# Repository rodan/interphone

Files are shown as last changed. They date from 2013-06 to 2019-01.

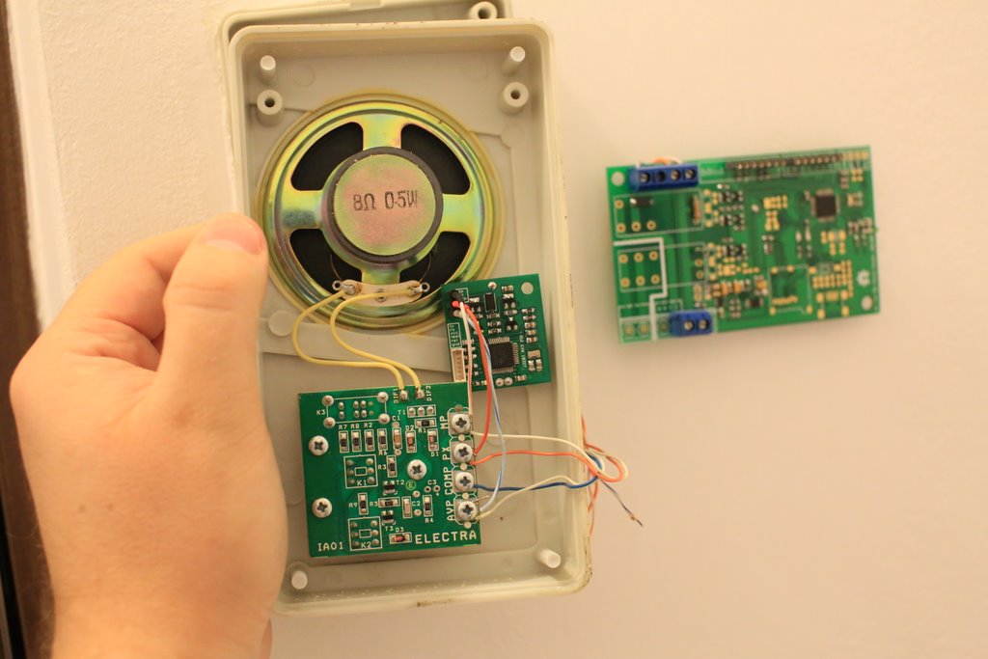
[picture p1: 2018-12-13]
img/DA0B7957.JPG

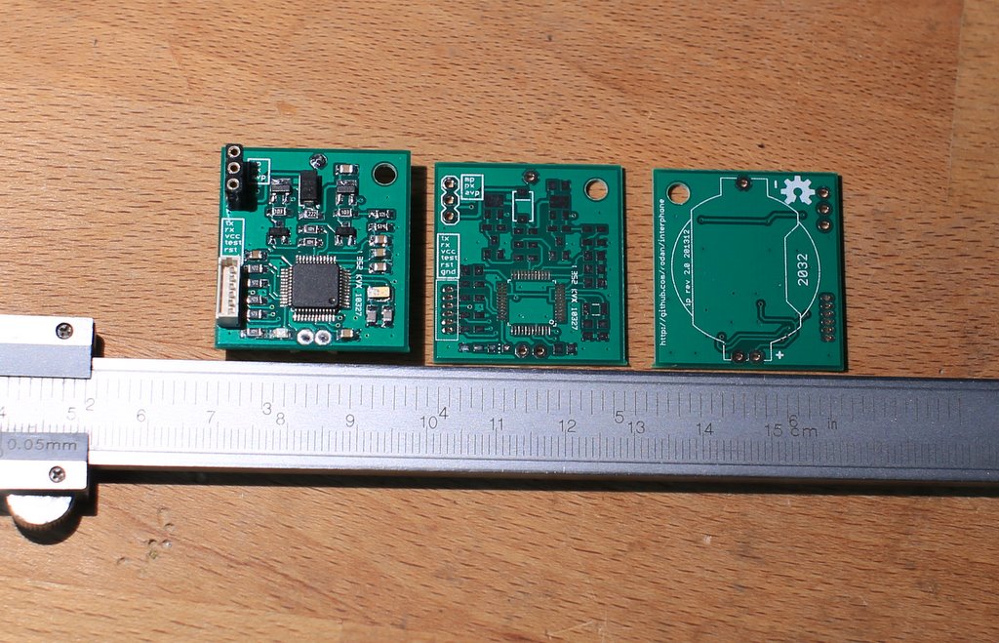
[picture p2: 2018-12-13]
img/DA0B7967.JPG

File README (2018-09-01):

MSP430F5510 based project that ties into the appartment interphone system. in this case it's an Electra IA01.
it allows the owner outside the building to open the door by following a pre-determined list of actions.

if config.h RADIO option (*) is defined then the door opening is triggered by the following actions:
 - call interphone number
 - wait 2s
 - send a radio signal to a receiver that is tied into the project. the receiver should pull P1.2 low on activation.
 - door opens if the signal was received in the defined time window
 If the radio option is not viable due to poor signal/noise ratio another scenario is implemented by deactivating the RADIO ifdef.
 - call interphone number
 - hang up and call again in the software predetermined timeframe
 - door opens

 the first scenario needs one 12v battery, a 12V one channel RC receiver and transmitter. a chronos watch could be used as the RC remote if the topology permits, see [1], [2]. current consumption is about 110uA@12V.
 the second scenario only needs one 3v 2032 Li cell. current consumption is about 1.4uA@3V. the pcb for this one is to be found in hardware/ip_simple.brd

Pinout:
 - P1.1 - 'ring' detector from interphone 'PX'
 - P1.2 - (optional) radio trigger
 - P1.4 - OPEN
 - P1.5 - TALK
 - P1.6 - (optional) power enable for radio rx system

(*) radio-related code removed

 homepage:        https://github.com/rodan/interphone
 author:          Petre Rodan <2b4eda@subdimension.ro>
 license:         GNU GPLv3
 parts of the code were originally forked from the openchronos-ng project [3]. 

 software requirements:

   msp430 toolchain

[1] http://www.ti.com/tool/ez430-chronos
[2] https://github.com/rodan/openchronos-rfsw
[3] http://openchronos-ng.sourceforge.net

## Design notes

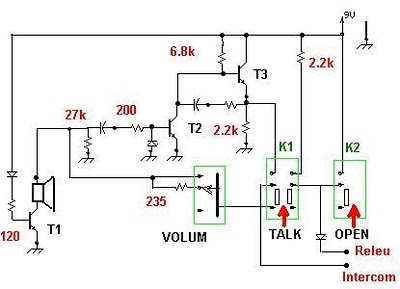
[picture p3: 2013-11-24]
img/electra.jpg

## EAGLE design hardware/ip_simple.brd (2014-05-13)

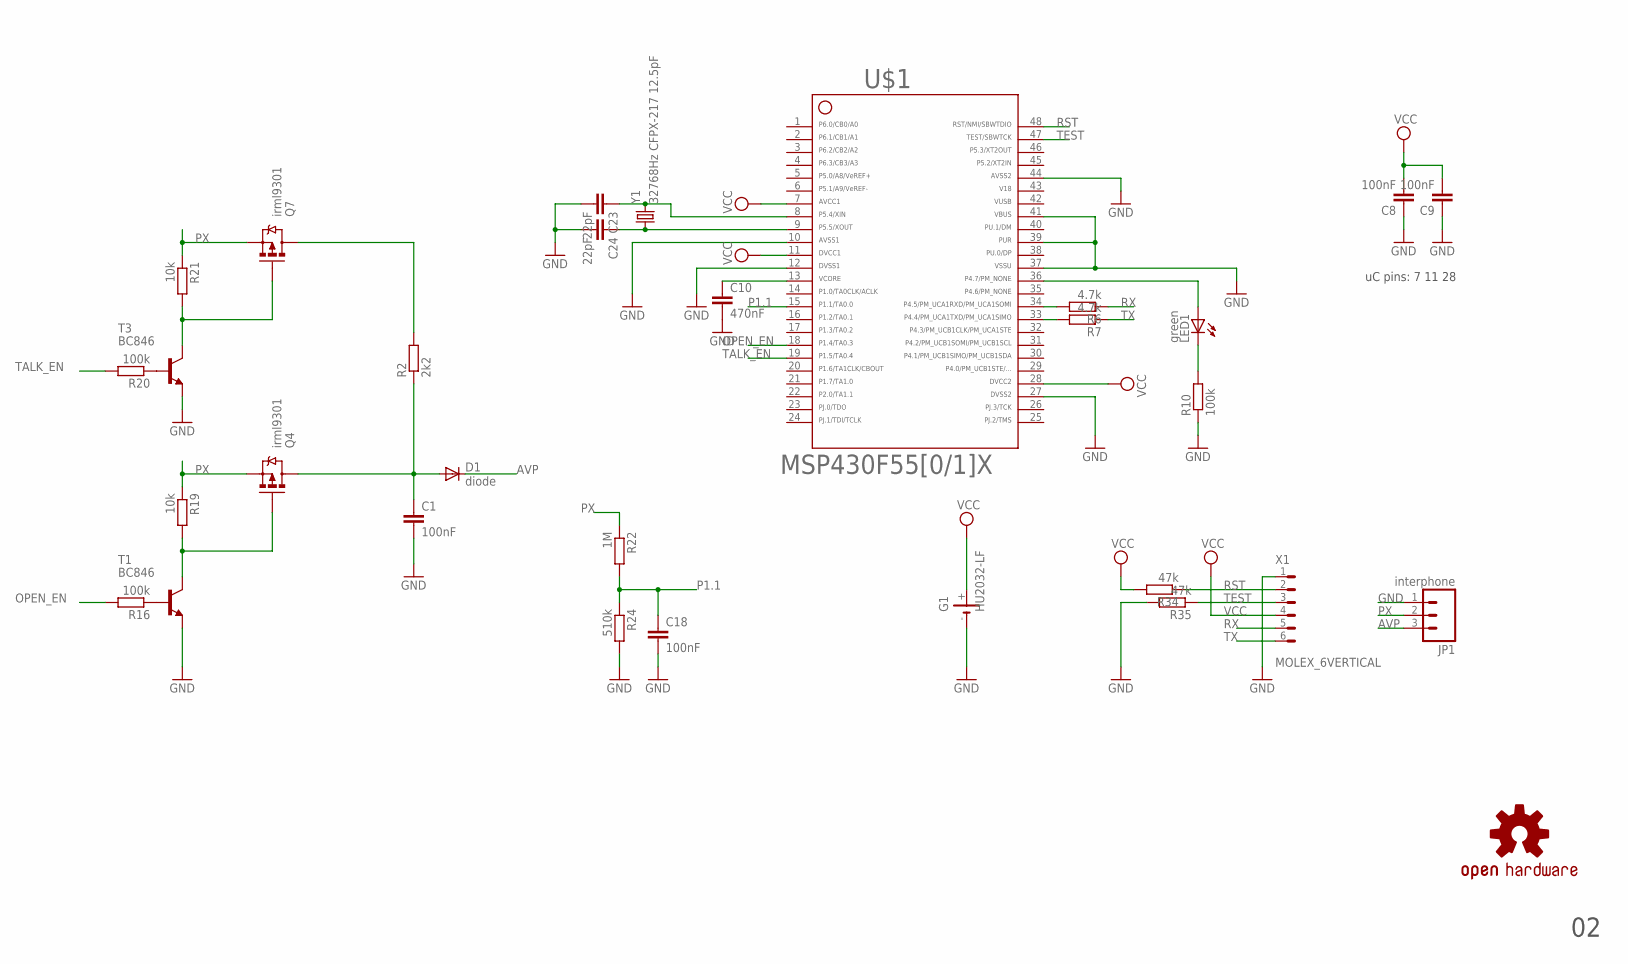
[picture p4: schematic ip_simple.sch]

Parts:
C1, C8, C9, C18: 100nF; C0805
C10: 470nF; C0805
C23, C24: 22pF; C0805
D1: diode; SMA-DIODE
G1: HU2032-LF
JP1: interphone; 1X03
LED1: green; CHIP-LED0805
Q4, Q7: irml9301; SOT23-3_POWER
R2: 2k2; R0805W
R6, R7: 4.7k; R0805W
R10, R16, R20: 100k; R0805W
R19, R21: 10k; R0805W
R22: 1M; R0805W
R24: 510k; R0805W
R34, R35: 47k; R0805W
T1, T3: BC846; SOT23
U$1: F55[0/1]X---PT48; PT48
U$7: OSHW-LOGOM; OSHW-LOGO-M
X1: MOLEX_6VERTICAL; 0530470610
Y1: 32768Hz CFPX-217 12.5pF; CRYSTAL-SMD-3.2X1.5

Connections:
42: U$1.42
43: U$1.43
46: U$1.46
AVP: D1.C, JP1.3
GND: C1.2, C8.1, C9.1, C10.2, C18.2, C23.2, C24.2, G1.-, JP1.1, R10.1, R24.2, R35.2, T1.2 (E), T3.2 (E), U$1.10, U$1.12, U$1.27, U$1.37, U$1.39, U$1.41, U$1.44, X1.1
LED: LED1.A, U$1.36
unnamed: LED1.C, R10.2
unnamed: R16.1, T1.1 (B)
unnamed: C1.1, D1.A, Q4.3 (D), R2.1
unnamed: Q7.3 (D), R2.2
unnamed: C10.1, U$1.13
unnamed: R6.2, U$1.34
unnamed: R7.2, U$1.33
unnamed: C24.1, U$1.9, Y1.P$1 (1)
unnamed: C23.1, U$1.8, Y1.P$2 (2)
unnamed: Q4.1 (G), R19.2, T1.3 (C)
unnamed: R20.1, T3.1 (B)
unnamed: Q7.1 (G), R21.2, T3.3 (C)
OPEN_EN: R16.2, U$1.18
P1.1: C18.1, R22.2, R24.1, U$1.15
PX: JP1.2, Q4.2 (S), Q7.2 (S), R19.1, R21.1, R22.1
RST: R34.1, U$1.48, X1.2
RX: R6.1, X1.5
TALK_EN: R20.2, U$1.19
TEST: R35.1, U$1.47, X1.3
TX: R7.1, X1.6
VCC: C8.2, C9.2, G1.+, R34.2, U$1.7, U$1.11, U$1.28, X1.4

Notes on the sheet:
uC pins: 7 11 28

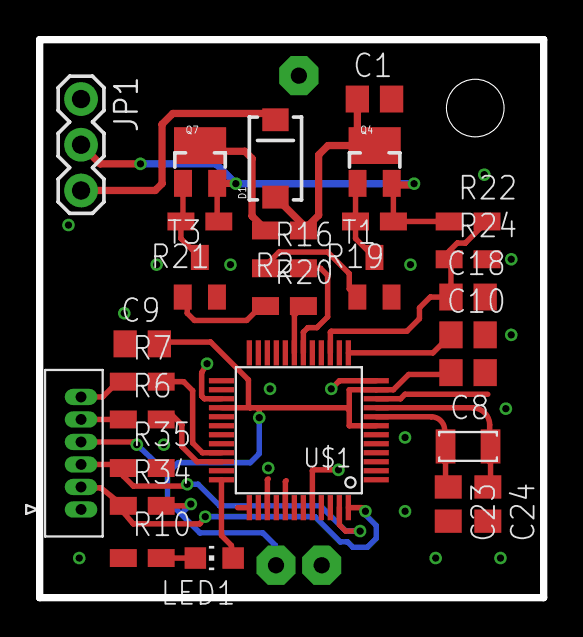
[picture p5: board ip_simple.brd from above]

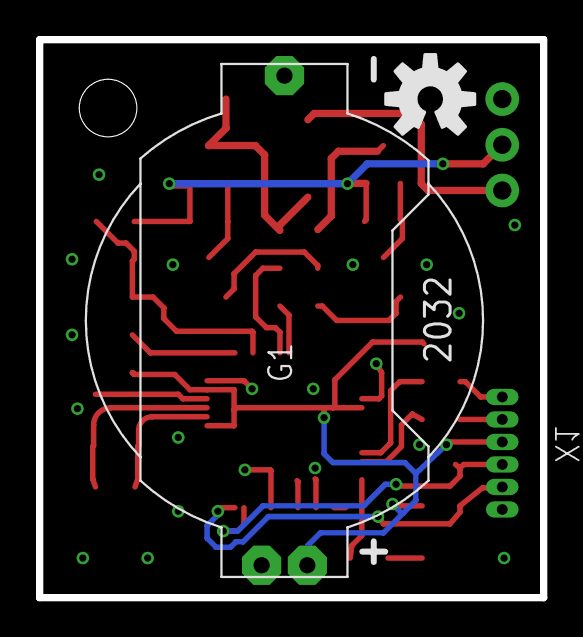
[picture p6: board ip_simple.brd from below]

Board: 2 copper layers, 28.0 x 31.0 mm, 31 parts (2 on the bottom side), 24 nets.

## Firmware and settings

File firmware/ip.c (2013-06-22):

//  MSP430F5510 based project that ties into the appartment interphone system. 
//  in this case it's an Electra IA01.
//  it allows the owner outside the building to open the door by following a 
//  pre-determined list of actions.
//
//  author:          Petre Rodan <petre.rodan@simplex.ro>
//  available from:  https://github.com/rodan/
//  license:         GNU GPLv3

#include <stdio.h>
#include <string.h>

#include "ip.h"
#include "calib.h"
#include "drivers/sys_messagebus.h"
#include "drivers/pmm.h"
#include "drivers/rtc.h"
#include "drivers/timer_a0.h"
#include "drivers/uart.h"
#include "drivers/adc.h"

volatile uint8_t trigger1;

// TRIG1 is the 9V input trigger (interphone cable 'PX')
// tied to P1.1
#define TRIG1 BIT1

#ifdef RADIO
// TRIG2 is the radio control trigger. active low.
// tied to P1.2
#define TRIG2 BIT2
volatile uint8_t trigger2;
#endif

uint32_t last_trigger;

char str_temp[64];

#ifdef CALIBRATION
static void do_calib(enum sys_message msg)
{
    uint16_t q_bat = 0;
    float v_bat;

    adc10_read(0, &q_bat, REFVSEL_2);
    v_bat = q_bat * VREF_2_5 * DIV_BAT;
    adc10_halt();

    //1023 22.22DA0
    snprintf(str_temp, 13, "%4d %02d.%02d\r\n",
             q_bat, (uint16_t) v_bat / 100, (uint16_t) v_bat % 100);
    uart_tx_str(str_temp, strlen(str_temp));

}
#endif                          // CALIBRATION

int main(void)
{
    main_init();
    //uart_init();

#ifdef CALIBRATION
    sys_messagebus_register(&do_calib, SYS_MSG_RTC_SECOND);
#endif

    //snprintf(str_temp, 4, "?\r\n");
    //uart_tx_str(str_temp, strlen(str_temp));

    while (1) {
        sleep();
        __no_operation();
        wake_up();
#ifdef USE_WATCHDOG
        WDTCTL = (WDTCTL & 0xff) | WDTPW | WDTCNTCL;
#endif
        check_events();
    }
}

void main_init(void)
{
    //uint16_t timeout = 5000;

    // watchdog triggers after 4 minutes when not cleared
#ifdef USE_WATCHDOG
    WDTCTL = WDTPW + WDTIS__8192K + WDTSSEL__ACLK + WDTCNTCL;
#else
    WDTCTL = WDTPW + WDTHOLD;
#endif
    SetVCore(3);

    P5SEL |= BIT5 + BIT4;

    P1SEL = 0x0;
    P1DIR = 0xf9;
    P1OUT = 0x00;

    // IRQ triggers on rising edge
    P1IES &= ~TRIG1;
    // Reset IRQ flags
    P1IFG &= ~TRIG1;
    // Enable button interrupts
    P1IE |= TRIG1;

#ifdef RADIO
    P1REN |= TRIG2;  // enable internal resistance
    P1OUT |= TRIG2;  // set as pull-up resistance
    P1IES |= TRIG2;  // Hi/Lo edge
    P1IFG &= ~TRIG2; // IFG cleared
    trigger2 = false;
#endif

    P2SEL = 0x0;
    P2DIR = 0x1;
    P2OUT = 0x0;

    P3SEL = 0x0;
    P3DIR = 0x1f;
    P3OUT = 0x0;

    P4SEL = 0x00;
    P4DIR = 0xb9;
    P4OUT = 0x0;

    //P5SEL is set above
    P5DIR = 0x0;
    P5OUT = 0x0;

    P6SEL = 0x1;
    P6DIR = 0x00;
    P6REN = 0x0a;

    PJOUT = 0x00;
    PJDIR = 0xFF;

#ifdef CALIBRATION
    // send MCLK to P4.0
    __disable_interrupt();
    // get write-access to port mapping registers
    //PMAPPWD = 0x02D52;
    PMAPPWD = PMAPKEY;
    PMAPCTL = PMAPRECFG;
    // MCLK set out to 4.0
    P4MAP0 = PM_MCLK;
    //P4MAP0 = PM_RTCCLK;
    PMAPPWD = 0;
    __enable_interrupt();
    P4DIR |= BIT0;
    P4SEL |= BIT0;

    // send ACLK to P1.0
    P1DIR |= BIT0;
    P1SEL |= BIT0;
#endif

    rtca_init();
    timer_a0_init();
    trigger1 = false;
    last_trigger = -1L;
}

void sleep(void)
{
    // disable VUSB LDO and SLDO
    USBKEYPID = 0x9628;
    USBPWRCTL &= ~(SLDOEN + VUSBEN);
    USBKEYPID = 0x9600;
    _BIS_SR(LPM3_bits + GIE);
    __no_operation();
}

void wake_up(void)
{

#ifdef RADIO
    uint8_t tries = 0;
    uint16_t q_bat = 0;
    float v_bat;
    adc10_read(0, &q_bat, REFVSEL_2);
    v_bat = q_bat * VREF_2_5 * DIV_BAT;
    adc10_halt();

    if (trigger1 && (v_bat > 1200)) {
        snprintf(str_temp, 13, "trig1 high\r\n");
        uart_tx_str(str_temp, strlen(str_temp));
        r_enable;
        timer_a0_delay(100000);
        P1IFG &= ~TRIG1;
        P1IE &= ~TRIG1;
        //trigger2 = false;
        P1IFG &= ~TRIG2;
        P1IE |= TRIG2;
        timer_a0_delay_noblk(1000000);
        while (tries < 10) {
            if (timer_a0_last_event & TIMER_A0_EVENT_CCR2) {
                timer_a0_last_event &= ~TIMER_A0_EVENT_CCR2;
                timer_a0_delay_noblk(1000000);
                tries++;
                snprintf(str_temp, 7, "t %2d\r\n",tries);
                uart_tx_str(str_temp, strlen(str_temp));
            }
            if (trigger2) {
                // debounce
                timer_a0_delay(50000);
                if (P1IN & TRIG2) {
                    continue;
                }
                P1IE &= ~TRIG2;
                snprintf(str_temp, 7, "open\r\n");
                uart_tx_str(str_temp, strlen(str_temp));
                r_disable;
                open_door();
                break;
            }
        }
        r_disable;
        P1IFG &= ~TRIG2;
        P1IE &= ~TRIG2;
        trigger1 = false;
        trigger2 = false;
        P1IE |= TRIG1;
    } else
#endif
    if (trigger1) {
        // debounce
        timer_a0_delay(50000);
        if ((P1IN & TRIG1) == 0) {
            return;
        } else {
            //sprintf(str_temp, "trig1 %ld\r\n", rtca_time.sys);
            //uart_tx_str(str_temp, strlen(str_temp));
            if (rtca_time.sys - last_trigger < 5) {
                P1IE &= ~TRIG1;
                //snprintf(str_temp, 7, "open\r\n");
                //uart_tx_str(str_temp, strlen(str_temp));
                open_door();
                P1IE |= TRIG1;
            }
            last_trigger = rtca_time.sys;
        }
        trigger1 = false;
    }
}

void check_events(void)
{
    struct sys_messagebus *p = messagebus;
    enum sys_message msg = 0;

    // drivers/rtca
    if (rtca_last_event) {
        msg |= rtca_last_event;
        rtca_last_event = 0;
    }
    while (p) {
        // notify listener if he registered for any of these messages
        if (msg & p->listens) {
            p->fn(msg);
        }
        p = p->next;
    }
}

void open_door(void)
{
    // 0.2 0.1 0.1 0.1 is working
    //P4OUT |= BIT3; // orange led on
    timer_a0_delay(100000);
    talk_enable;
    timer_a0_delay(100000);
    //P4OUT &= ~BIT3; // orange led off
    talk_disable;
    timer_a0_delay(100000);
    //P4OUT |= BIT7; // green led on
    open_enable;
    timer_a0_delay(100000);
    //P4OUT &= ~(BIT3 + BIT7); // leds off
    open_disable;
}

#pragma vector=PORT1_VECTOR
__interrupt void Port_1(void)
{
    if (P1IFG & TRIG1) {
        trigger1 = true;
        P1IFG &= ~TRIG1;
        _BIC_SR_IRQ(LPM3_bits);
    }

#ifdef RADIO
    else if (P1IFG & TRIG2) {
        trigger2 = true;
        P1IFG &= ~TRIG2;
        _BIC_SR_IRQ(LPM3_bits);
    }
#endif
}

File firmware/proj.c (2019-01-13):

//  MSP430F5510 based project that ties into the appartment interphone system. 
//  in this case it's an Electra IA01.
//  it allows the owner outside the building to open the door by following a 
//  pre-determined list of actions.
//
//  author:          Petre Rodan <2b4eda@subdimension.ro>
//  available from:  https://github.com/rodan/
//  license:         GNU GPLv3

#include <stdio.h>
#include <string.h>
#include "proj.h"
#include "drivers/sys_messagebus.h"
#include "drivers/timer_a0.h"

// the period in which a second trigger is expected, in timer A0 ticks.
// ticks = time(sec) * 32768
#define period_min 120000
#define period_max 150000

// an integer representing the time after which the uC will go into LPM4 standby
// standby_time(sec) = standby_time(int) * 2sec
// (2sec is the overflow time of TA0R)
#define standby_time 10

// TRIG1 is the 9V input trigger (interphone cable 'PX')
// tied to P1.1
#define TRIG1 BIT1

volatile uint8_t trigger1;
uint32_t last_trigger;

#ifdef CONFIG_DEBUG
#include "drivers/uart1.h"
char str_temp[64];
#endif

static void timer_a0_irq(enum sys_message msg)
{
    if (timer_a0_ovf >= standby_time) {
        // disable TA0 so that LPM4 can have maximum effectiveness
        TA0CTL = 0;
#ifdef USE_WATCHDOG
        WDTCTL = WDTPW + WDTHOLD;
#endif
        _BIS_SR(LPM4_bits + GIE);
        __no_operation();

        // a PORT1 irq just came in, so we wake up
        timer_a0_init();
#ifdef USE_WATCHDOG
    WDTCTL = WDTPW + WDTIS__512K + WDTSSEL__ACLK + WDTCNTCL;
#endif
        trigger1 = false;
        last_trigger = 0;
    }
}

int main(void)
{
    main_init();
#ifdef CONFIG_DEBUG
    uart1_init();
#endif

    sys_messagebus_register(&timer_a0_irq, SYS_MSG_TIMER0_IFG);

    while (1) {
        // sleep
        _BIS_SR(LPM3_bits + GIE);
        __no_operation();
        wake_up();
#ifdef USE_WATCHDOG
        WDTCTL = (WDTCTL & 0xff) | WDTPW | WDTCNTCL;
#endif
        check_events();
    }
}

void main_init(void)
{
    // watchdog triggers after 25sec when not cleared
#ifdef USE_WATCHDOG
    WDTCTL = WDTPW + WDTIS__512K + WDTSSEL__ACLK + WDTCNTCL;
#else
    WDTCTL = WDTPW + WDTHOLD;
#endif
    P5SEL |= BIT5 + BIT4;

    P1SEL = 0;
    P1DIR = 0xfd;
    P1OUT = 0;

    // IRQ triggers on rising edge
    P1IES &= ~TRIG1;
    // Reset IRQ flags
    P1IFG &= ~TRIG1;
    // Enable button interrupts
    P1IE |= TRIG1;

    P2SEL = 0;
    P2DIR = 0x1;
    P2OUT = 0;

    P3SEL = 0;
    P3DIR = 0x1f;
    P3OUT = 0;

    P4SEL = 0;
    P4DIR = 0xff;
    P4OUT = 0;

    //P5SEL is set above
    P5DIR = 0xff;
    P5OUT = 0;

    P6DIR = 0xff;
    P6OUT = 0;

    PJDIR = 0xff;
    PJOUT = 0;

    // disable VUSB LDO and SLDO
    USBKEYPID = 0x9628;
    USBPWRCTL &= ~(SLDOEN + VUSBEN);
    USBKEYPID = 0x9600;

    timer_a0_init();
    trigger1 = false;
    last_trigger = 0;
}

void wake_up(void)
{
    uint32_t trig_time, trig_diff;
    if (trigger1) {
        // debounce
        timer_a0_delay(50000);
        if ((P1IN & TRIG1) == 0) {
            return;
        } else {
            trig_time = ((uint32_t) timer_a0_ovf << 16) + (uint16_t) TA0R;
            trig_diff = trig_time - last_trigger;
#ifdef CONFIG_DEBUG
            sprintf(str_temp, "trig1 %ld %ld\r\n", trig_time, trig_diff);
            uart1_tx_str(str_temp, strlen(str_temp));
#endif
            if ((trig_diff > period_min) && (trig_diff < period_max)) {
                P1IE &= ~TRIG1;
#ifdef CONFIG_DEBUG
                snprintf(str_temp, 7, "open\r\n");
                uart1_tx_str(str_temp, strlen(str_temp));
#endif
                open_door();
                P1IE |= TRIG1;
            }
            last_trigger = trig_time;
        }
        trigger1 = false;
    }
}

void check_events(void)
{
    struct sys_messagebus *p = messagebus;
    enum sys_message msg = 0;

    // drivers/timer_a0
    if (timer_a0_last_event) {
        msg |= timer_a0_last_event << 7;
        timer_a0_last_event = 0;
    }

    while (p) {
        // notify listener if he registered for any of these messages
        if (msg & p->listens) {
            p->fn(msg);
        }
        p = p->next;
    }
}

void open_door(void)
{
    timer_a0_delay(100000);
    talk_enable;
    timer_a0_delay(100000);
    talk_disable;
    timer_a0_delay(100000);
    open_enable;
    timer_a0_delay(100000);
    open_disable;
}

// Port 1 interrupt service routine
#if defined(__TI_COMPILER_VERSION__) || defined(__IAR_SYSTEMS_ICC__)
#pragma vector=PORT1_VECTOR
__interrupt void Port_1(void)
#elif defined(__GNUC__)
__attribute__ ((interrupt(PORT1_VECTOR)))
void Port1_ISR(void)
#else
#error Compiler not supported!
#endif
{
    if (P1IFG & TRIG1) {
        trigger1 = true;
        P1IFG &= ~TRIG1;
        LPM4_EXIT;
    }
}

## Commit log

2013-11-22 add sch+brd for the simple scenario
    [ip_simple.brd, ip_simple.sch]
2013-11-22 sent to manufacturer
    [ip_simple.brd]
2013-11-24 fix ADC REFVSEL bug
2013-12-20 fix wrong pin in README
    [ip_extra.brd, ip_extra.sch]
2013-12-21 rev 2
    [ip_simple.brd, ip_simple.sch]
2014-01-18 revision 2
    [adc_calibration.xls]
2014-05-13 cleanup for unused pins
    [ip_simple.brd, ip_simple.sch]

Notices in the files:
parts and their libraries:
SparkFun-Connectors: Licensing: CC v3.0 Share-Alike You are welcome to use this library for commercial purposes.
